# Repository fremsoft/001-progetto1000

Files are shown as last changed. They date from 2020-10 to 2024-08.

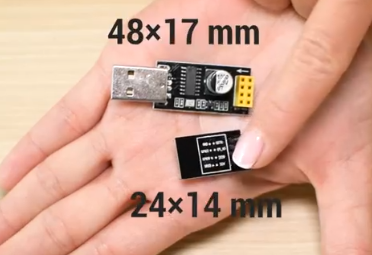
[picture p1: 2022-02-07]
Doc/WIFI/esp-usb.png

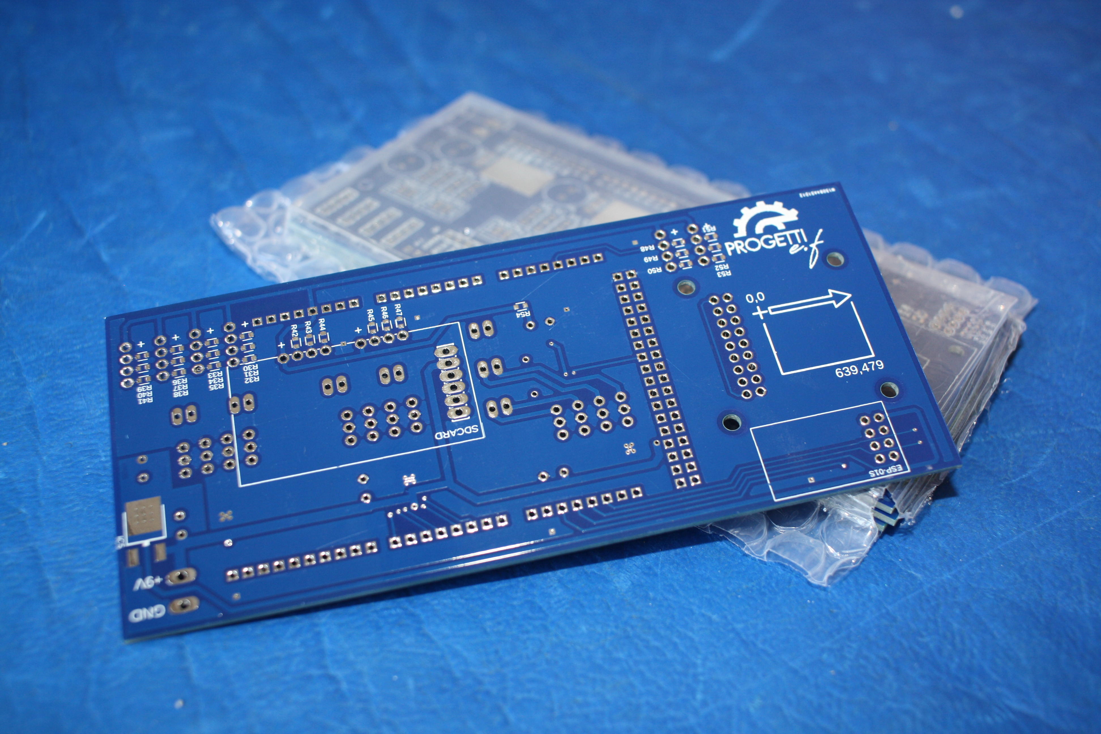
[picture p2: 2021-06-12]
Fusion360/Shield-p1000-2021-05-20/Doc/p1000_bottom.jpg

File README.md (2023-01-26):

# #progetto1000 il Robot che risolve il Cubo di Rubik
Questo è il primo progetto del [:arrow_forward: Canale YouTube "PROGETTI con Emanuele Frisoni"](https://youtube.com/c/fremsoft), un progetto collaborativo che nasce al raggiungimento di 1000 iscritti: [:movie_camera: Guarda la Playlist completa del progetto](https://www.youtube.com/watch?v=VcB0eAnL97o&list=PLxAafib4pWc7LSfuXC9RSEif6I1dyx5FP)

1. [Parte la progettazione in Live Streaming su Twitch](README.md#parte-la-progettazione-in-live-streaming-su-twitch)
2. [Definizione delle specifiche](README.md#definizione-delle-specifiche)
3. [Attività da svolgere e svolte](README.md#attivit%C3%A0-da-svolgere-e-svolte)
4. [Codici sorgenti](README.md#codici-sorgenti)
5. [Sostieni PROGETTO1000](README.md#sostieni-progetto1000)
6. [Lista della spesa](README.md#lista-della-spesa)

   6.1 [Attrezzature da laboratorio e Kit](README.md#attrezzature-da-laboratorio-e-kit)
   
   6.2 [Materiale e schede elettroniche](README.md#materiale-e-schede-elettroniche)
   
   6.3 [Materiale vario per assemblaggio prototipo](README.md#materiale-vario-per-assemblaggio-prototipo)

## Parte la progettazione in Live Streaming su Twitch
**Ogni Giovedì sera alle 22:00** ci incontriamo su [Twitch Tv](https://www.twitch.tv/fremsoft) per progettare insieme il Robot che risolve il Cubo di Rubik, partendo da zero. Affronteremo tutti i passaggi in maniera approfondita. Ho deciso di utilizzare tecnologie che conosco "per sentito dire", ma su cui non ho mai lavorato. In questo modo vedrai tutto il processo che sta dietro alla ricerca di una soluzione. A differenza di altri progetti che trovi in rete, #progetto1000 non esiste ancora, lo possiamo creare insieme. 

Lo scopo non è mostrare al mondo quanto siamo bravi, ma mostrare agli aspiranti progettisti quali sono tutte le difficoltà che potranno incontrare nel loro percorso e suggerire un modo per affrontarle e superarle.

:clapper: Canale Twitch:  [https://www.twitch.tv/fremsoft](https://www.twitch.tv/fremsoft)

[^ Torna su](README.md#progetto1000-il-robot-che-risolve-il-cubo-di-rubik)

## Definizione delle specifiche
Siccome si tratta di un progetto collaborativo, per definire le specifiche di progetto sono stati fatti alcuni sondaggi esplorativi per determinare quali tecnologie utilizzare in questo primo progetto. I risultati del sondaggio sono i seguenti:

1. Arduino o Microchip PIC? **ARDUINO** [4 voti / 2]

2. Encoder Ottico o Accelerometro Gravitazionale? **ENCODER OTTICO** [3 voti / 1]

3. Costruzioni LEGO o Particolari stampati con Stampante 3D? **STAMPA 3D** [3 voti / 4]

4. Stand alone o Connesso a un PC/Smartphone? **SIA STANDALONE CHE COMANDATO** [4 voti / 4]

5. Muto o Sonoro? **SONORO** [3 voti / 4]

6. Cieco o con Telecamera? **TELECAMERA** [0 voti / 4]

7. Procedurale o Intelligenza Artificiale? **A.I.** [0 voti / 5 ]

[^ Torna su](README.md#progetto1000-il-robot-che-risolve-il-cubo-di-rubik)

## Attività da svolgere e svolte
Ogni progetto che si rispetti deve prevedere una serie di fasi da svolgere. Maggiore sarà la difficoltà del progetto e maggiori sono le incognite, tanto più sarà difficile riuscire a prevedere con esattezza tutte le fasi. Ciononostante, è sempre buona norma prevedere con la massima accuratezza tutte le fasi del progetto in una sorta di planning. Ad ogni modo il progetto può essere periodicamente rivisitato, modificato e corretto, in corso d'opera.

L'utilità di suddividere il progetto in attività elementari, consente al progettista di avere un approccio più razionale ed evitare di disperdersi. Inoltre, laddove sia possibile lavorare in Team, la suddivisione del progetto in attività consente di stabilire se alcune attività possano essere svolte simultaneamente da più attori, per esempio dopo aver definito le specifiche di progetto con precisione, si può affidare il progetto meccanico ad un Team ed il progetto elettronico ad un altro Team di sviluppatori.

- [x] [Analisi di fattibilità](https://youtu.be/We6UntzGp7k)
- [x] Raccolta della documentazione e prove sperimentali con prototipi
  - [x] Dimensioni meccaniche e forze necessarie a manipolare il cubo di Rubik
  - [x] Caratteristiche elettriche e meccaniche dei motori c.c.
  - [x] Caratteristiche elettriche del driver (ponte-H) per motori c.c.
  - [x] Specifiche elettriche dei sensori ottici (fotoresistori/TCUT1350x01)
  - [x] Funzionamento di Arduino (uscite PWM, uscite parallele, timers)
  - [x] DAC e amplificatore audio per speaker 8 ohm
  - [x] Slot per Micro SD Card per Arduino per storage file audio
  - [x] Funzionamento Chip Camera OV7670 e acquisizione immagini
  - [x] Ottica del sensore OV7670
  - [x] Funzionamento del modulo WiFi per comunicazione con Smartphone
  - [x] Alimentazione 5V @ 10A
  - [-] ~~Selezione molle per mano robotica~~
- [x] Progettazione meccanica 
  - [x] Realizzazione delle parti che compongono il Robot (esportati in STL)
  - [x] Stampare in 3D le componenti meccaniche
  - [x] Assemblare le parti meccaniche con le parti elettriche (motori, encoder, etc)
- [x] Progettazione elettronica
   - [x] Alimentazione
   - [x] Shield p1000 
     - [x] DAC e Amplificatore per altoparlante
     - [x] Modulo SD-Card
     - [x] Interfacciamento Chip Camera OV7670
     - [x] Modulo WiFi
     - [x] Circuiti di condizionamento dei sensori ottici
     - [x] Comando motori
     - [x] Protezioni e filtri EMC/EMI
     - [x] Montare i componenti elettronici
     - [x] Collaudo generale dell'elettronica
- [ ] Progettazione del programma su Arduino
  - [ ] Movimentazione elementare (attraverso la porta seriale invieremo i comandi per eseguire i movimenti)
  - [ ] Acquisizione delle immagini da telecamera per distinguere i colori e mappare gli elementi del cubo di Rubik
  - [ ] Implementare gli algoritmi del metodo CFOP semplificato
    - [ ] Croce bianca
    - [ ] Faccia bianca e primo strato
    - [ ] Secondo strato
    - [ ] Croce gialla
    - [ ] OLL
    - [ ] PLL (primo passaggio)
    - [ ] PLL (secondo passaggio)
    - [ ] Allineamento terzo strato 
  - [ ] Implementare i suoni
- [ ] Progettazione della rete neurale
  - [ ] Addestramento di una rete neurale per riconoscere tutti gli OLL e PLL
  - [ ] Implementazione della rete neurale nell'algoritmo 
- [ ] Progettazione dell'applicativo per Android per mescolare il cubo con una specifica scramble o altro (forse questa fase salta)
- [ ] Dare un nome al robot

[^ Torna su](README.md#progetto1000-il-robot-che-risolve-il-cubo-di-rubik)

## Codici sorgenti
**#progetto1000** è un progetto Open-Source collaborativo. Tutti i sorgenti elaborati in fase di progettazione sono presenti su questo canale GitHub. Esplora le cartelle di [001-progetto1000](https://github.com/fremsoft/001-progetto1000) e troverai i sorgenti del progetto meccanico, elettronico, software e altro materiale prodotto in fase di progettazione.

Il codice sorgente di **Arduino** sarà disponibile anche a questo link: [Sorgenti Arduino](https://create.arduino.cc/editor/fremsoft/6501effc-6729-46f5-a2f1-0bfa0e9eb691/preview)

La Shield #P1000 è stata omaggiata da [PcbWay.com](https://www.pcbway.com/setinvite.aspx?inviteid=15084) che è sponsor ufficiale di Progetto 1000. Trovi il progetto del PCB scaricabile anche qui: [Shield #P1000 su PcbWay](https://www.pcbway.com/project/shareproject/Shield__P1000__for_Arduino_Mega.html), ricordati di votare il progetto!

[^ Torna su](README.md#progetto1000-il-robot-che-risolve-il-cubo-di-rubik)

## Sostieni PROGETTO1000 
Se **#progetto1000** ti sta appassionando e desideri sostenere la progettazione, puoi acquistare i componenti necessari alla creazione del prototipo o le attrezzature necessarie all'allestimento del laboratorio, facendoli recapitare al mio indirizzo. La lista dei desideri completa dove trovi tutte le cose che servono:

:notebook: "Wish list Amazon" - https://amzn.to/2BDtwIV

Un altro modo per sostenere il canale è seguendo il [canale YouTube](https://youtube.com/c/fremsoft), semplicemente guardando i video, iscrivendoti al canale, mettendo like e interagendo con i commenti, ma soprattutto condividendo i video che preferisci con i tuoi amici progettisti, sono tutti modi per sostenere gratuitamente il canale.

[^ Torna su](README.md#progetto1000-il-robot-che-risolve-il-cubo-di-rubik)

## Lista della spesa
**#progetto1000** sta nascendo, non abbiamo ancora una BOM (Bill Of Material), ma stiamo già acquistando un po' di materiale per realizzare il prototipo e fare le prime prove pratiche. Se vuoi sviluppare insieme a noi e vuoi eseguire le stesse prove a casa tua, ti indico quale materiale ho acquistato qui di seguito:

### Attrezzature da laboratorio e Kit
* [Kit Elettronico con breadboard](https://amzn.to/2QTgOw7)
* [Super Starter Kit UNO project](https://amzn.to/2QJrnNc)
* [Calibro digitale](https://amzn.to/36QMR6w)
* [Bilancia digitale](https://amzn.to/3nxseCa)

### Materiale e schede elettroniche
* [Arduino Mega 2560](https://amzn.to/30RCvj6)
* [Telecamera a colori per Arduino](https://amzn.to/3nbS0Ma)
* [Set 6 motori con accessori](https://amzn.to/3nhQrfy)
* [Fotoresistore](https://amzn.to/370EtBg)
* [Shield #P1000 su PcbWay](https://www.pcbway.com/project/shareproject/Shield__P1000__for_Arduino_Mega.html)

### Materiale vario per assemblaggio prototipo
* [Sfere in acciaio 4mm](https://amzn.to/3lzfDwr)

Trovi la lista completa al seguente link:
🛒 [Lista della spesa di #progetto1000](https://www.amazon.it/hz/wishlist/ls/8D7WPLCAZ7KL?tag=p-ef-21)

[^ Torna su](README.md#progetto1000-il-robot-che-risolve-il-cubo-di-rubik)

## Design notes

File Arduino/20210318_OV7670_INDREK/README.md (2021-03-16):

Queste sono alcune immagini catturate dalla Chip Camera OV7670 e salvate in formato HTML per essere visualizzate da un qualsiasi browser.

Finalmente riusciamo a distinguere qualcosa, le immagini sono parecchio sfocate ma siamo sulla buona strada:

1. [160x120_cubo_mischiato.htm](http://htmlpreview.github.io/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)

2. [160x24_cubo_1.htm](http://htmlpreview.github.io/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)

3. [160x24_cubo_2.htm](http://htmlpreview.github.io/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)
 
4. [160x24_cubo_3.htm](http://htmlpreview.github.io/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)

5. [160x24_cubo_azzurro.htm](http://htmlpreview.github.io/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)
 
6. [160x24_cubo_rosso.htm](http://htmlpreview.github.io/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)

7. [img1.htm](http://htmlpreview.github.io/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)

8. [img2.htm](http://htmlpreview.github.io/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)

9. [img3.htm](http://htmlpreview.github.io/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)

10. [img4.htm](http://htmlpreview.github.io/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)

11. [img5.htm](http://htmlpreview.github.io/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)

12. [img6.htm](http://htmlpreview.github.io/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)

13. [img7.htm](http://htmlpreview.github.io/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)

14. [img8.htm](http://htmlpreview.github.io/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)

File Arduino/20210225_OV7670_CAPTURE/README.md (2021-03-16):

Queste sono alcune immagini catturate dalla Chip Camera OV7670 e salvate in formato HTML per essere visualizzate da un qualsiasi browser.

Come ben visibile dal risultato prodotto, dobbiamo ancora lavorarci su affinché possiamo ottenere delle immagini accettabili:

1. [img.html](http://htmlpreview.github.io/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)

2. [blue.html](http://htmlpreview.github.io/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)

3. [nero.html](http://htmlpreview.github.io/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)

4. [rosso.html](http://htmlpreview.github.io/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)

5. [panna.html](http://htmlpreview.github.io/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)

6. [progetti.html](http://htmlpreview.github.io/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)

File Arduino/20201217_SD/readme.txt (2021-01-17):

Per usare questo Sketch occorre il MicroSD Card Adapter a slitta:

"Il Manuale di Arduino (Paolo Aliverti)" - https://amzn.to/39o6DaB
"Scheda Micro SD per Arduino" - https://amzn.to/34uBorh
"Micro SD Card 16 GB" - https://amzn.to/34y9N8x
"USB to SD Card Adapter" - https://amzn.to/2LZ575r

Vedi lo schema e la procedura qui: https://youtu.be/E36JJB-z9BE

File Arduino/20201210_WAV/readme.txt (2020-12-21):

Per usare questo Sketch occorre realizzare un DAC con 
rete a partitore resistivo R-2R sui pin 42(MSb)÷49(LSb)
di Arduino Mega.

Vedi lo schema qui: https://youtu.be/YSctt-mZF6c

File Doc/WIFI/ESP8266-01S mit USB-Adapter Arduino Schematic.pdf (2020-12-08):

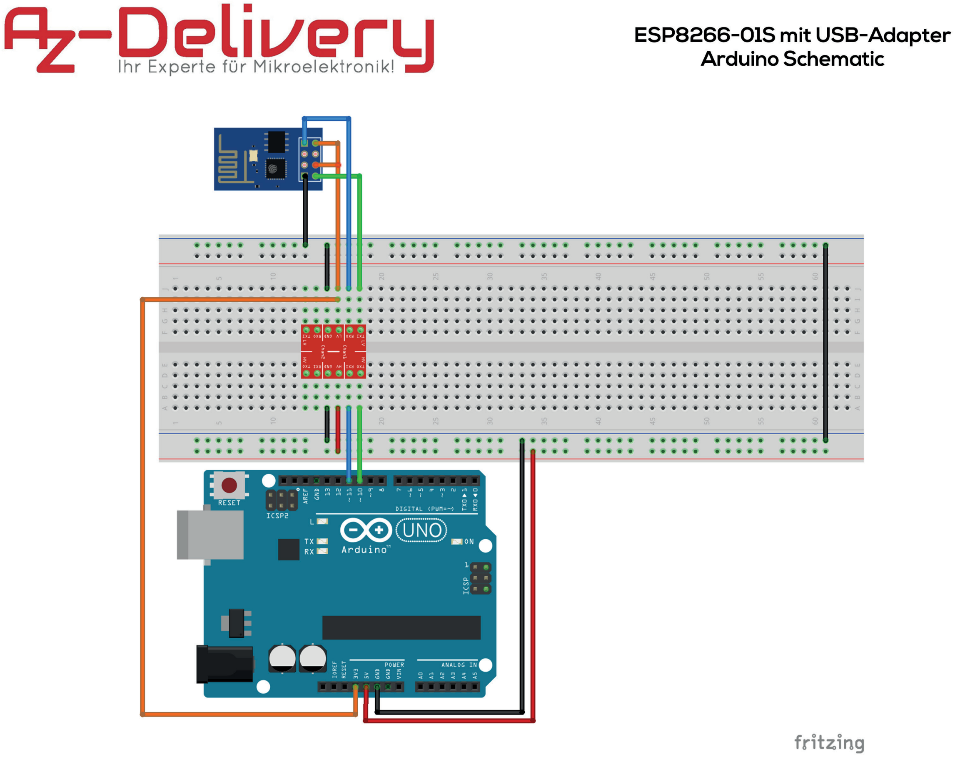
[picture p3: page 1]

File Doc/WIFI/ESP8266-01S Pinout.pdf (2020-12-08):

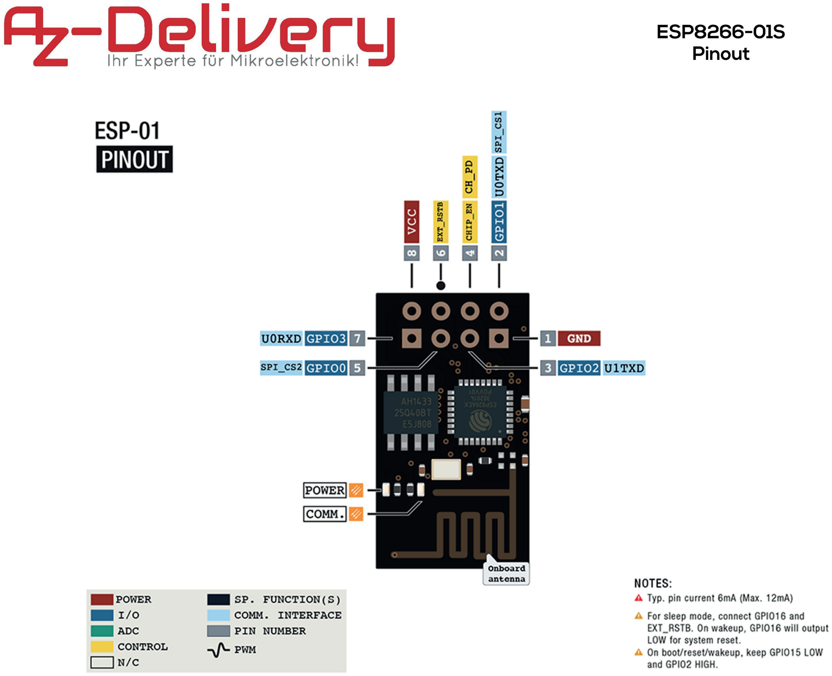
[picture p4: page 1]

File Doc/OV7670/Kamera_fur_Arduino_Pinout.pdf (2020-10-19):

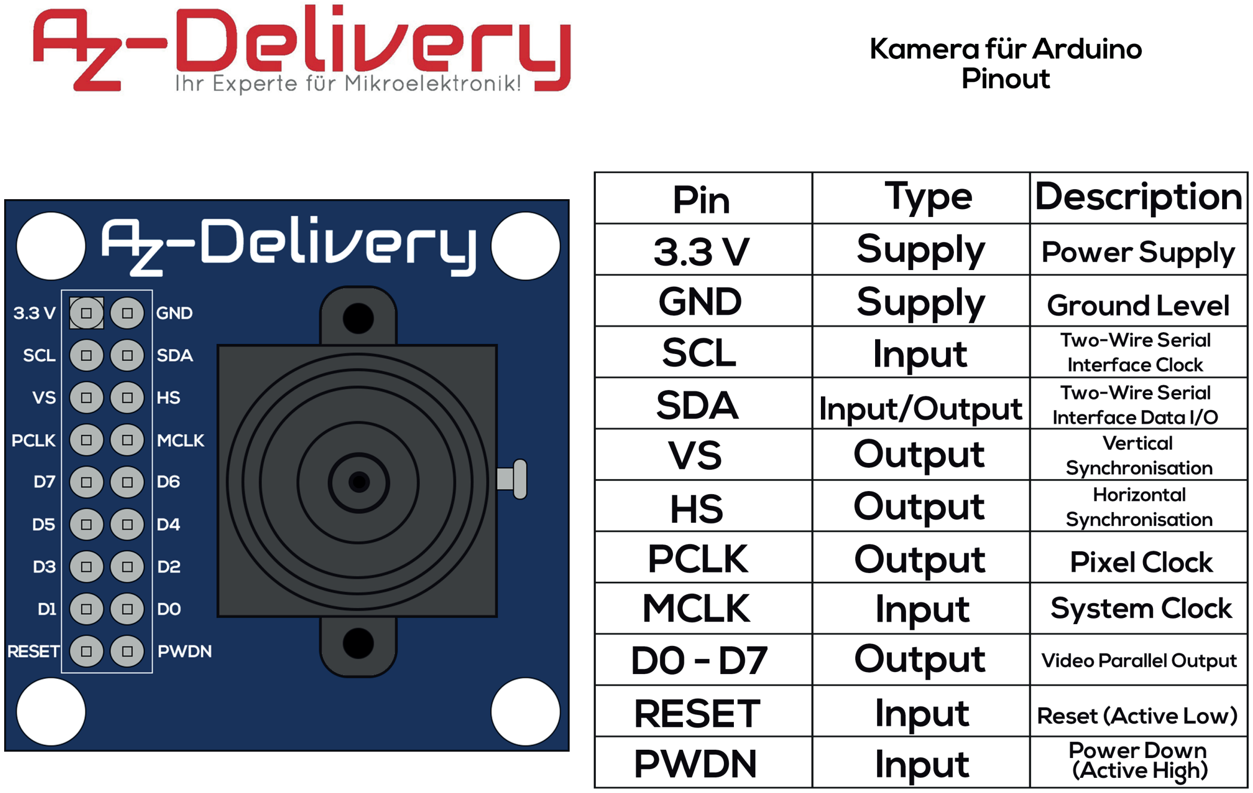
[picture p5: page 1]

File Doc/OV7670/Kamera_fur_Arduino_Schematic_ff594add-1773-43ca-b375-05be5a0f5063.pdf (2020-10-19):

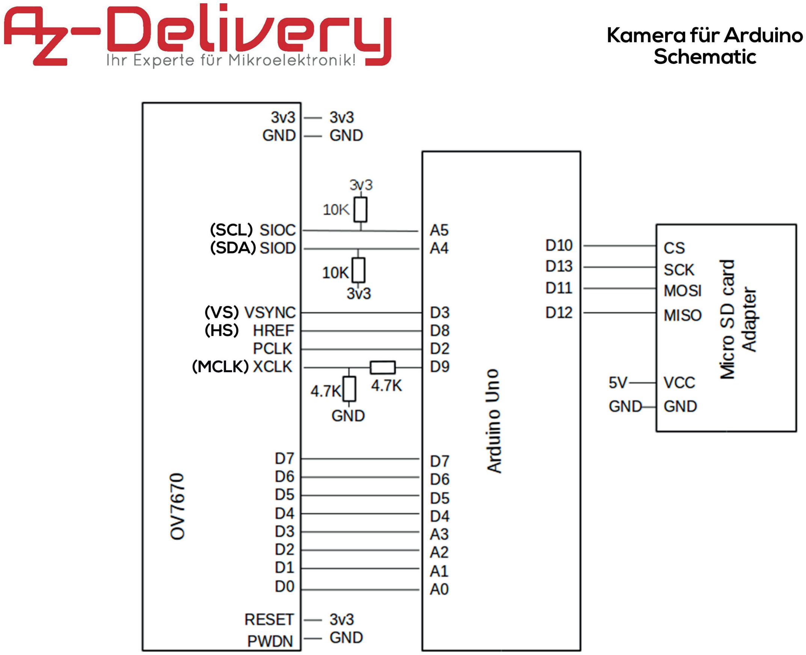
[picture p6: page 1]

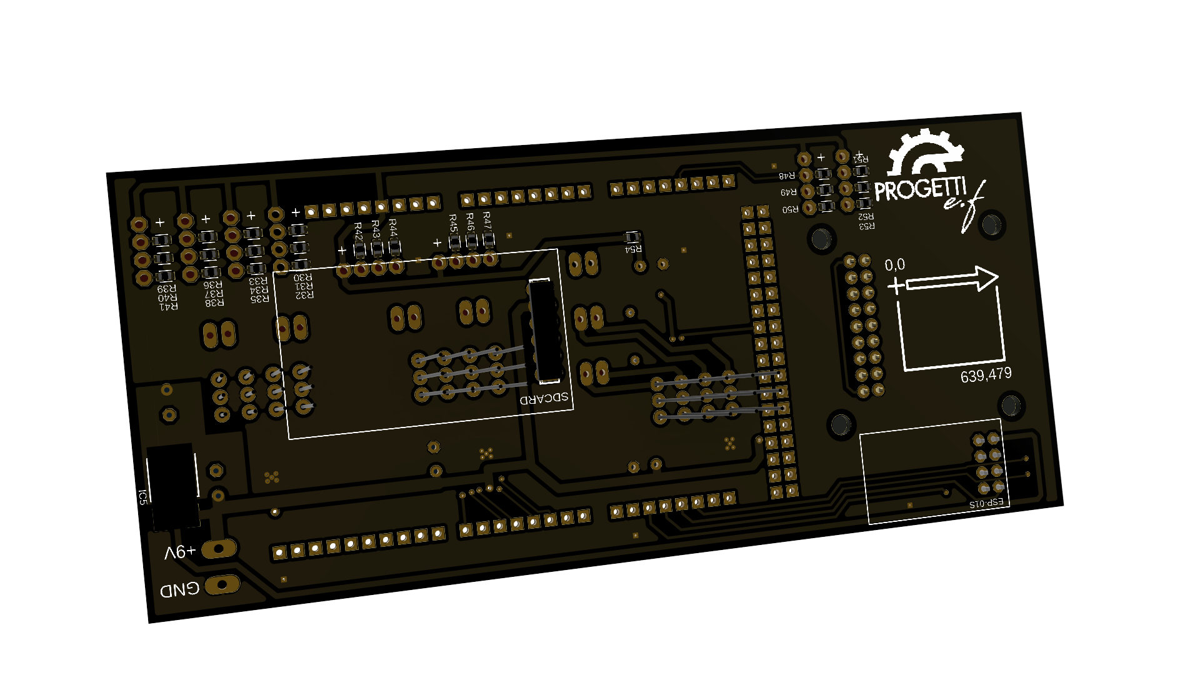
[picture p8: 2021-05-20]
Fusion360/Shield-p1000-2021-05-20/Doc/shield-p1000-render-bot.png

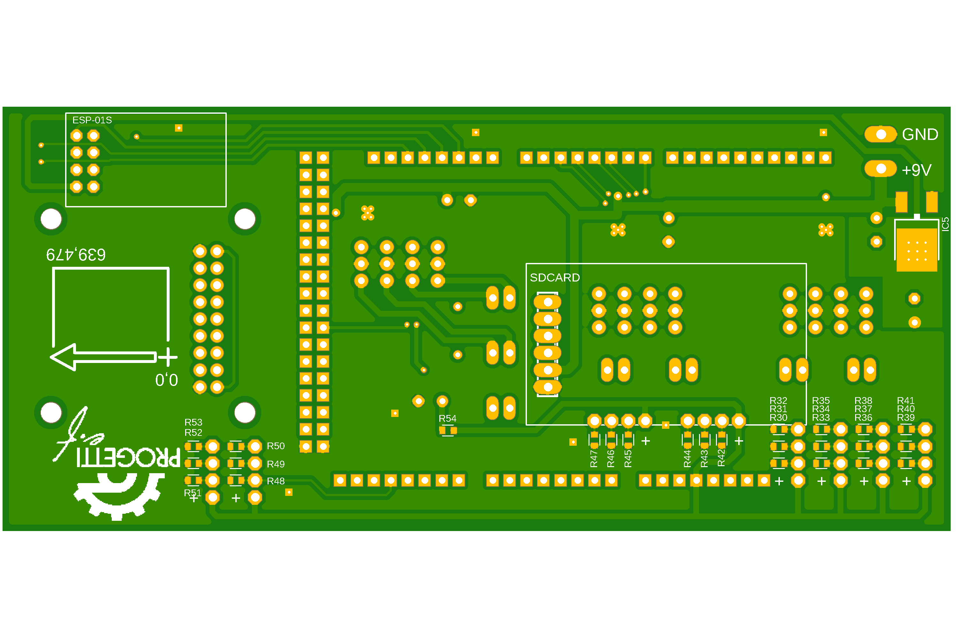
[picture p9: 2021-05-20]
Fusion360/Shield-p1000-2021-05-20/Doc/shield-p1000-bot.png

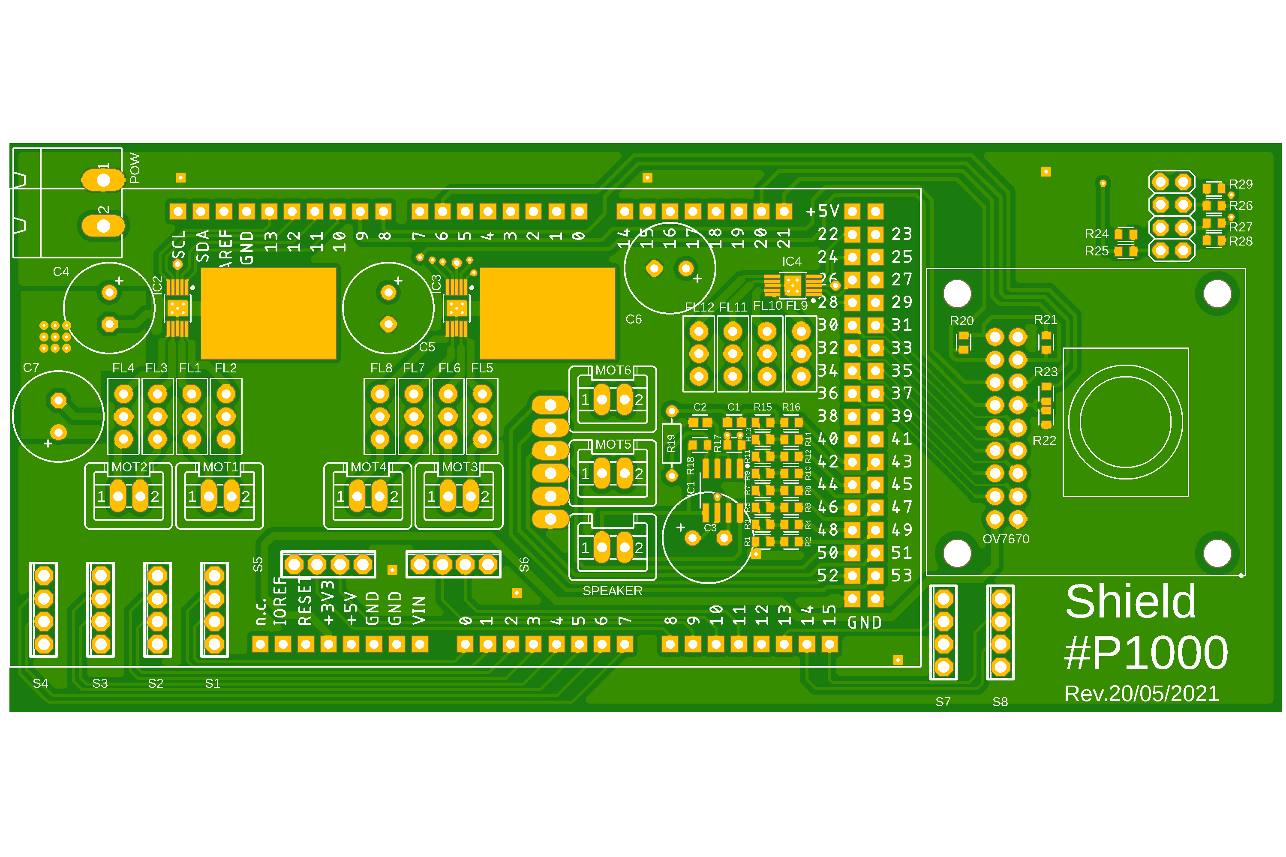
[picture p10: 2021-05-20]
Fusion360/Shield-p1000-2021-05-20/Doc/shield-p1000-top.png

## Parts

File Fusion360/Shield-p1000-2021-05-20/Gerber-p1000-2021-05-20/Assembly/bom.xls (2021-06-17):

 | QUANTITY | PARTS | VALUE | DESCRIPTION | PACKAGE | URL
PTH
 | 10 | ARDUINO MEGA | 77311-820-36LF | CONN HEADER VERT 10POS 2.54MM L=20mm | 10 x 2,54 mm HEADER | https://www.digikey.it/product-detail/it/amphenol-icc-fci/77311-820-36LF/609-77311-820-36LF-ND/4404923
 | 4 | C3, C4, C5, C6 | 220 uF | CAP 220 UF 20% 35 V | D=10mm sp=3.5mm | https://www.digikey.it/product-detail/it/w%C3%BCrth-elektronik/860040574006/732-9217-1-ND/5729160
 | 1 | C7 | 100 uF | CAP 100 UF 20% 50 V | D=10mm sp=3.5mm | https://www.digikey.it/product-detail/it/w%C3%BCrth-elektronik/860010674014/732-8666-1-ND/5728621
 | 1 | ESP-01S | PPTC042LFBN-RC | CONN HDR 8POS 0.1 TIN PCB | 4x2 x 2.54 mm HEADER | https://www.digikey.it/product-detail/it/sullins-connector-solutions/PPTC042LFBN-RC/S7072-ND/810211
 | 12 | FL1, FL2, FL3, FL4, FL5, FL6, FL7, FL8, FL9, FL10, FL11, FL12 | DSS1NB32A101Q91A | FILTER LC(T) 100PF TH | PTH 3 x 2.54 MM | https://www.digikey.it/product-detail/it/murata-electronics/DSS1NB32A101Q91A/490-9787-1-ND/5018362
 | 7 | MOT1, MOT2, MOT3, MOT4, MOT5, MOT6, SPEAKER | JST-XH | XH-2A (PCB MALE), XH-2Y (FEMALE) | 2 x 2.54 mm HEADER | https://amzn.to/3yEI4QU
 | 1 | OV7670 | PPTC092LFBN-RC | CONN HDR 18POS 0.1 TIN PCB | 9x2 x 2.54 mm HEADER | https://www.digikey.it/product-detail/it/sullins-connector-solutions/PPTC092LFBN-RC/S7077-ND/810215
 | 1 | POWER | TBP01R1-508-02BE | TERMINAL BLOCK, PLUGGABLE, 5.08, PCB | 2 x 5.08 mm | https://www.digikey.it/product-detail/it/cui-devices/TBP01R1-508-02BE/102-6406-ND/10238383
 | 1 | POWER | TBP01P1-508-02BE | TERMINAL BLOCK, PLUGGABLE, 5.08 | 2 x 5.08 mm | https://www.digikey.it/product-detail/it/cui-devices/TBP01P1-508-02BE/102-6390-ND/10238367
 | 1 | R19 | 10 kohm | RES 10K OHM 1/4W 5% AXIAL | 2,30 x 6,00 mm axial ¼ W | https://www.digikey.it/product-detail/it/stackpole-electronics-inc/CF14JT10K0/CF14JT10K0CT-ND/1830374
 | 8 | S1, S2, S3, S4, S5, S6, S7, S8 | JST-XH | XH-4A (PCB MALE), XH-4Y (FEMALE) | 4 x 2.54 mm HEADER | https://amzn.to/3yEI4QU
SMD
 | 2 | C1, C2 | 1 uF | CAP CER 1UF 25V X5R 0603 | CAPC1608X85 | https://www.digikey.it/product-detail/it/samsung-electro-mechanics/CL10A105KA8NNNC/1276-1102-1-ND/3889188
 | 1 | IC1 | LM4889MA | IC AMP CLASS AB MONO 1W 8SOIC | SOIC127P599X175-8N | https://www.digikey.it/product-detail/it/texas-instruments/LM4889MA-NOPB/296-43508-5-ND/947615
 | 3 | IC2, IC3, IC4 | A3909 | IC MOTOR DRIVER PAR 10MSOP | 10-MSOP | https://www.digikey.it/product-detail/it/allegro-microsystems/A3909GLYTR-T/620-1499-1-ND/3979660
 | 1 | IC5 | LD117ADT33TR | LDO VOLTAGE REGULATOR | TO-252-3 DPACK | https://www.digikey.it/product-detail/it/texas-instruments/LM1117IDT-3-3-NOPB/LM1117IDT-3-3-NOPB-ND/482898
 | 9 | R1, R2, R4 ,R6, R8, R10, R12, R14, R16 | 20 kohm | RES 20K OHM 1% 1/10W 0603 | RESC1608X60 | https://www.digikey.it/product-detail/it/stackpole-electronics-inc/RMCF0603FT20K0/RMCF0603FT20K0CT-ND/1943075
 | 1 | R18 | 47 kohm | RES 47K OHM 1% 1/10W 0603 | RESC1608X60 | https://www.digikey.it/product-detail/it/bourns-inc/CR0603-FX-4702ELF/CR0603-FX-4702ELFCT-ND/3925317
 | 4 | R22, R24, R28, R29 | 1.2 kohm | RES SMD 1.2K OHM 1% 1/10W 0603 | RESC1608X60 | https://www.digikey.it/product-detail/it/bourns-inc/CR0603-FX-1201ELF/118-CR0603-FX-1201ELFCT-ND/3925300
 | 4 | R23, R25, R26, R27 | 680 ohm | RES SMD 680 OHM 1% 1/10W 0603 | RESC1608X60 | https://www.digikey.it/product-detail/it/te-connectivity-passive-product/CRGCQ0603F680R/A129686CT-ND/8577518
 | 10 | R3, R5, R7, R9, R11, R13, R15, R17, R20, R21 | 10 kohm | RES SMD 10K OHM 1% 1/4W 0603 | RESC1608X60 | https://www.digikey.it/product-detail/it/rohm-semiconductor/ESR03EZPF1002/RHM10KADCT-ND/1983753
 | 16 | R30, R31, R33, R34. R36, R37, R39, R40, R42, R43, R45, R46, R48, R49, R51, R52 | 4.7 kohm | RES 4.7K OHM 1% 1/10W 0603 | RESC1608X60 | https://www.digikey.it/product-detail/it/bourns-inc/CR0603-FX-4701ELF/CR0603-FX-4701ELFCT-ND/3740884
 | 8 | R32, R35, R38, R41, R44, R47, R50, R53 | 330 ohm | RES SMD 330 OHM 5% 1/10W 0603C | RESC1608X60 | https://www.digikey.it/product-detail/it/te-connectivity-passive-product/CRGCQ0603J330R/A130088CT-ND/8577920
 | 1 | R54 | 10 ohm | RES 10 OHM 1% 1/3W 0603 | RESC1608X60 | https://www.digikey.it/product-detail/it/koa-speer-electronics-inc/SG73P1JTTD10R0F/2019-SG73P1JTTD10R0FCT-ND/13404248
COMPONENTS
 | 1 | ARDUINO MEGA | ARDUINO MEGA | Arduino Mega 2560 R3 |  | https://amzn.to/2SraGMU
 | 1 | ESP-01S | ESP-01S | AZDelivery ESP-01S ESP8266 WiFi Module | 4x2 x 2.54 mm HEADER | https://amzn.to/3yAf5On
 | 2 | CABLE | CABLE | CBL 2COND 18AWG BLACK/RED 1M | 18AWG x 1m | https://www.digikey.it/product-detail/it/tensility-international-corp/30-00415/T1306-1-ND/5638247
 | 6 | CM1, CM2, CM3, CM4, CM5, CM6 | 100 nF | CAP CER 0.1UF 50V X7R AXIAL | AXIAL PTH | https://www.digikey.it/product-detail/it/vishay-beyschlag-draloric-bc-components/A104K15X7RF5TAA/1109PHCT-ND/145913
 | 1 | MICROSD | SD-0128 | AZDelivery MicroSD module | 6 x 2.54 mm HEADER | https://amzn.to/3vkUED2
 | 2 | MOT1, MOT2, MOT3, MOT4, MOT5, MOT6 | DC MOTOR KIT + GEARS | Proster 6 Set DC Motore DIY | 38 x 16 x 19 mm | https://amzn.to/3fIIbCy
 | 1 | OV7670 | OV7670 | AZDelivery OV7670 RGB Chip Camera | 9x2 x 2.54 mm HEADER | https://amzn.to/34cejJs
 | 1 | SPEAKER | SP-4005Y | SPEAKER, 88DB SENSITIVITY, 40MM | 40 mm | https://www.digikey.it/product-detail/it/soberton-inc/SP-4005Y/433-1270-ND/9924431

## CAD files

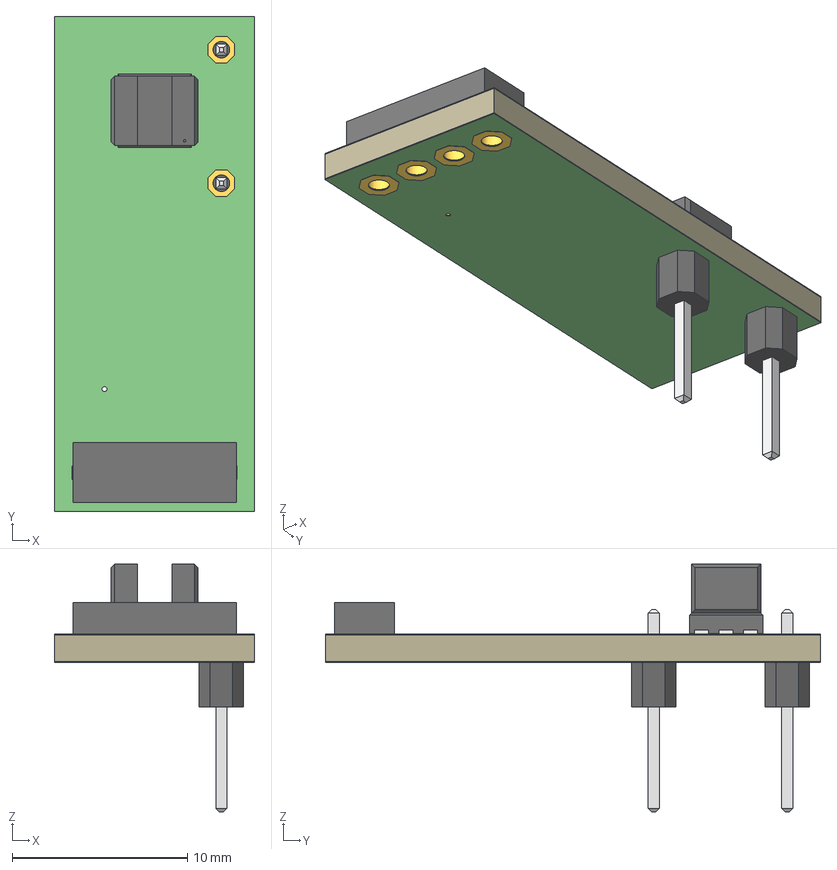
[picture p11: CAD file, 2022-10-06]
Fusion360/Encoder-p1000/ecnoder_TCUT1350 v3.step
11.4 x 28.2 x 14.1 mm
Board
4POL254
1X01 x 2
1-copper
16-copper
1-soldermask
16-soldermask

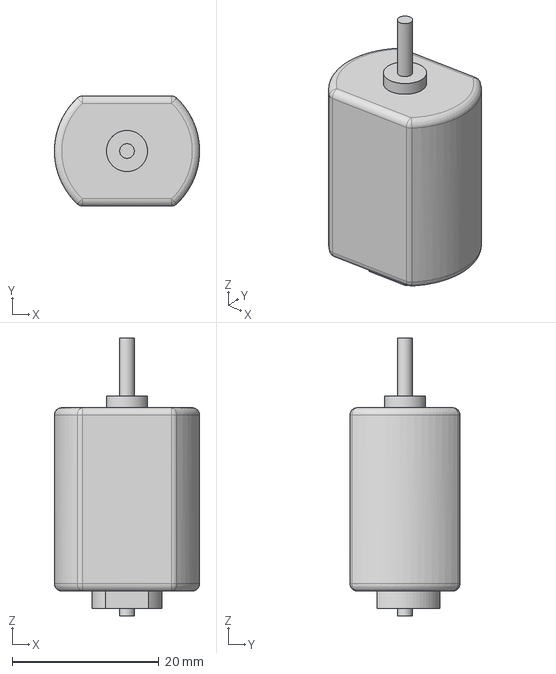
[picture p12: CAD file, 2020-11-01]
Fusion360/Motorino DC 3V v3.igs
19.8 x 15.0 x 37.9 mm

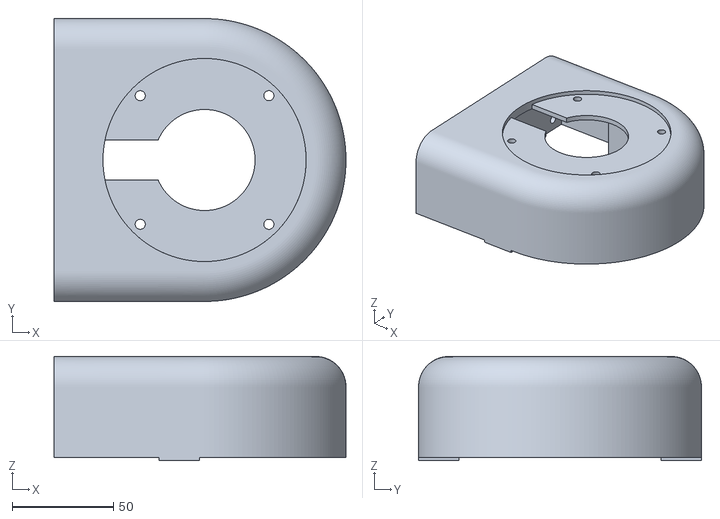
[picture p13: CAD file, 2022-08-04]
Fusion360/Robot_p1000/stl_produzione/basamento robot 2.stl
144.5 x 140.0 x 51.5

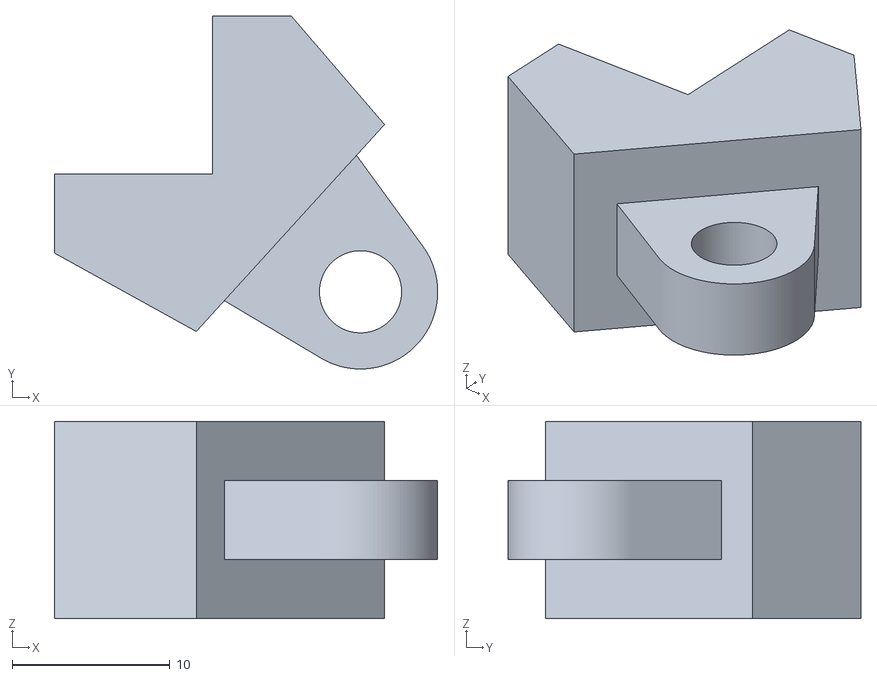
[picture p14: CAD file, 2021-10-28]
Fusion360/stl_mano_robotica/falangetta.stl
24.3 x 22.3 x 12.5

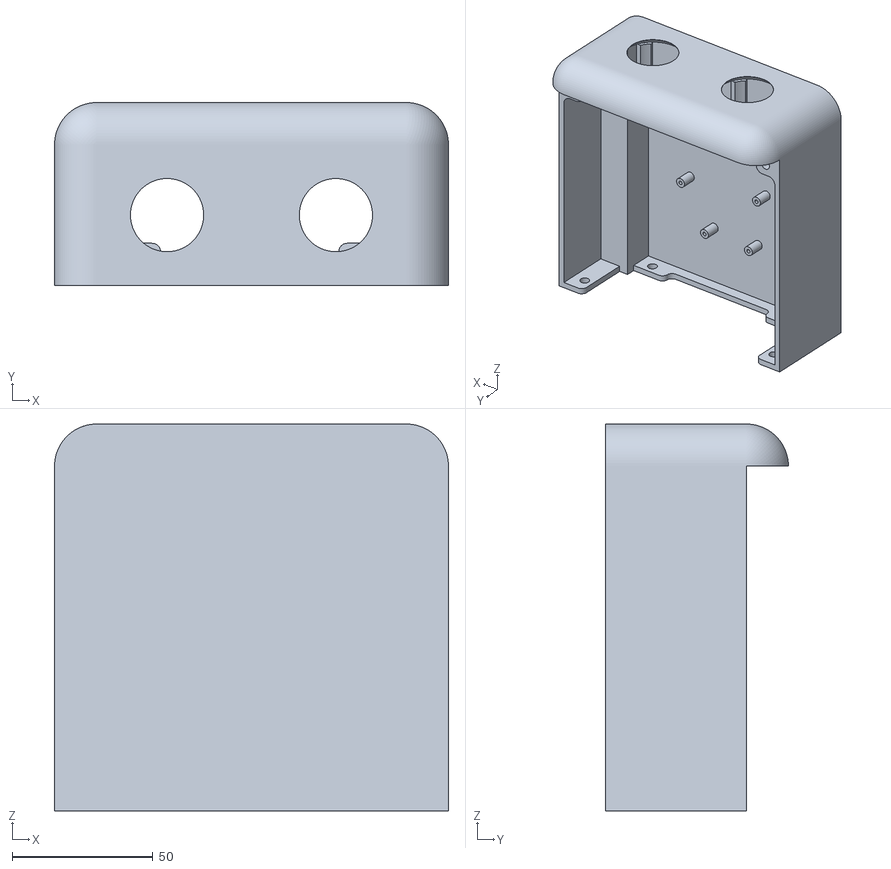
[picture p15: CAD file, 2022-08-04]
Fusion360/Robot_p1000/stl_produzione/basamento robot 5.stl
140.0 x 65.0 x 137.5

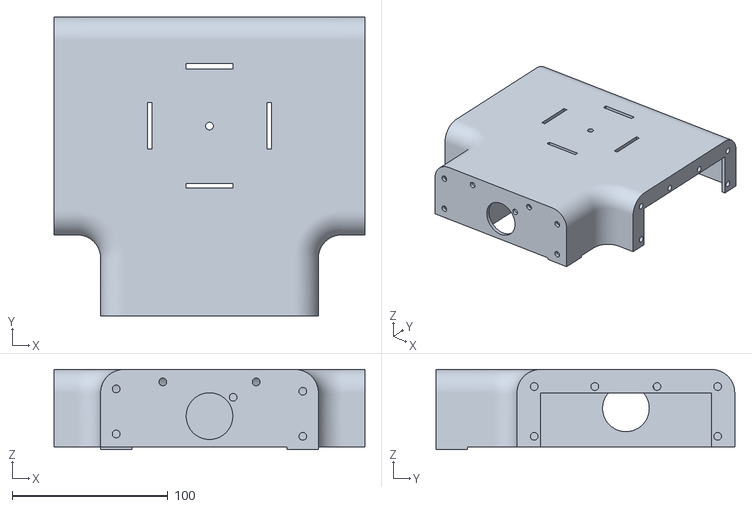
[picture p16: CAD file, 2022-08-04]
Fusion360/Robot_p1000/stl_produzione/basamento robot 1.stl
200.0 x 192.0 x 51.5

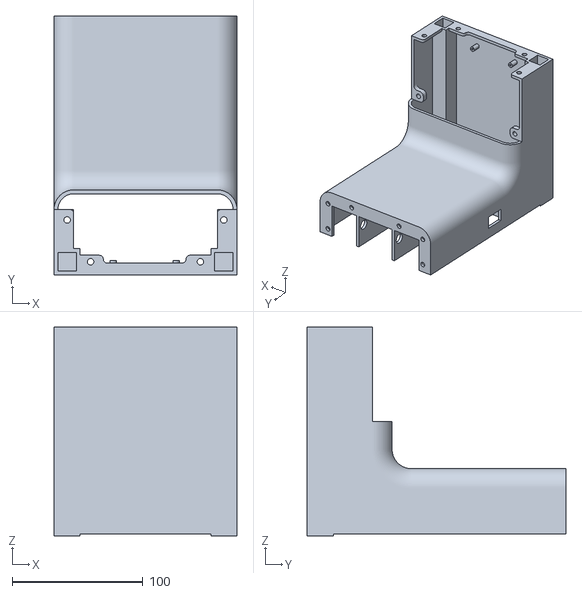
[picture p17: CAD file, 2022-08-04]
Fusion360/Robot_p1000/stl_produzione/basamento robot 4.stl
140.0 x 198.0 x 160.0

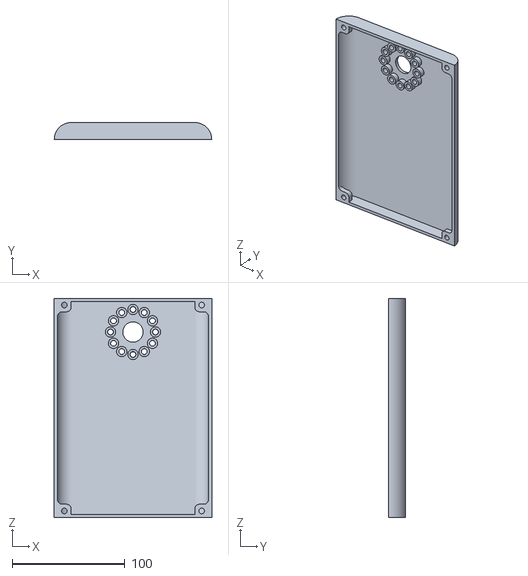
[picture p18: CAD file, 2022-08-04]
Fusion360/Robot_p1000/stl_produzione/basamento robot 6.stl
140.0 x 15.0 x 194.6

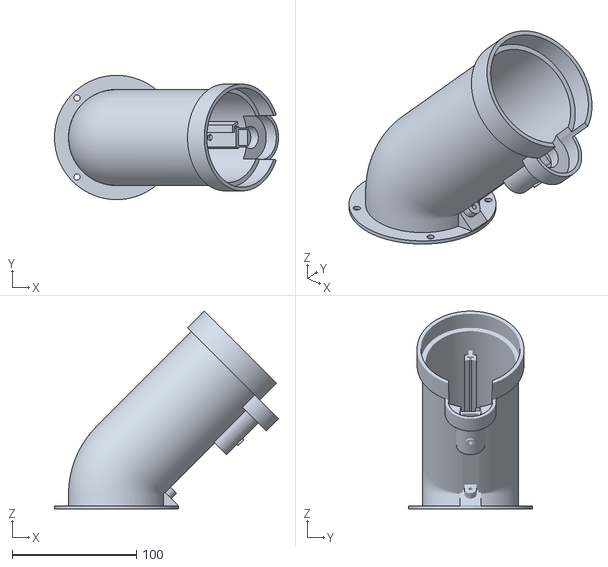
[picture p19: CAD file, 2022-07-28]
Fusion360/Robot_p1000/stl_produzione/braccio.stl
180.3 x 100.0 x 159.2

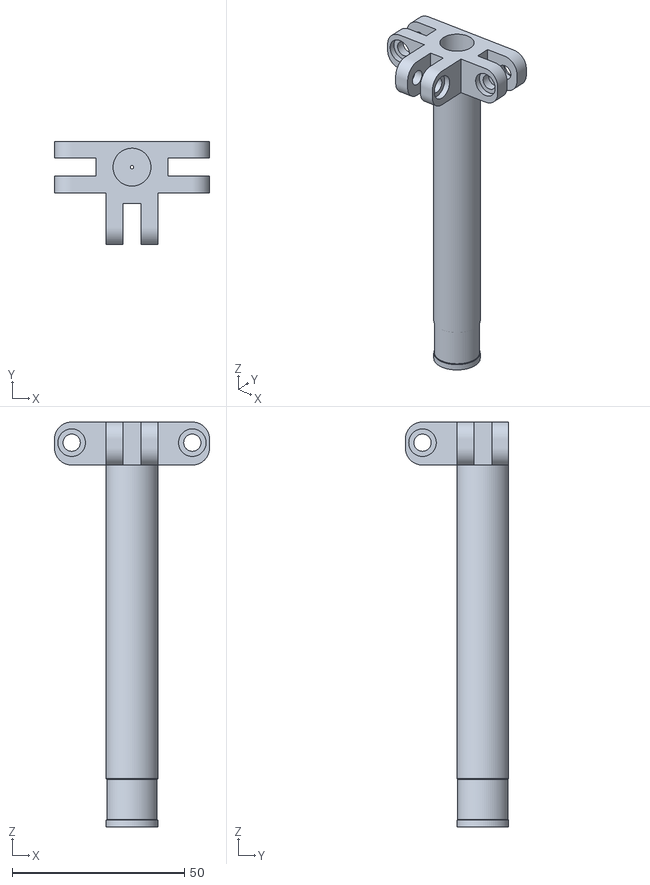
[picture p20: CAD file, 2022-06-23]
Fusion360/Robot_p1000/stl_produzione/martelletto.stl
45.0 x 30.0 x 117.5

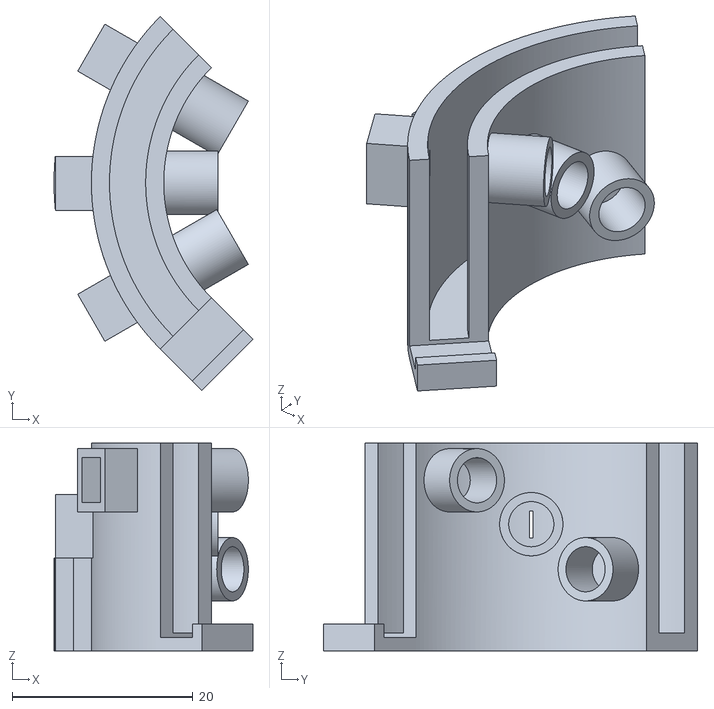
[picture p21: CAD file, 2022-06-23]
Fusion360/Robot_p1000/stl_produzione/mascherino_encoder.stl
22.0 x 41.4 x 23.0

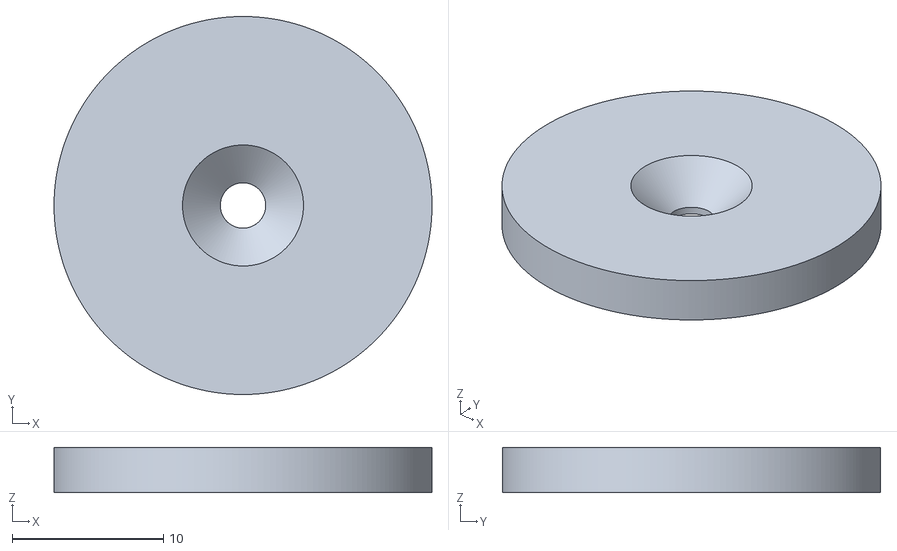
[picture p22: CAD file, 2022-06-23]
Fusion360/Robot_p1000/stl_produzione/rondella-martelletto.stl
25.0 x 25.0 x 3.00

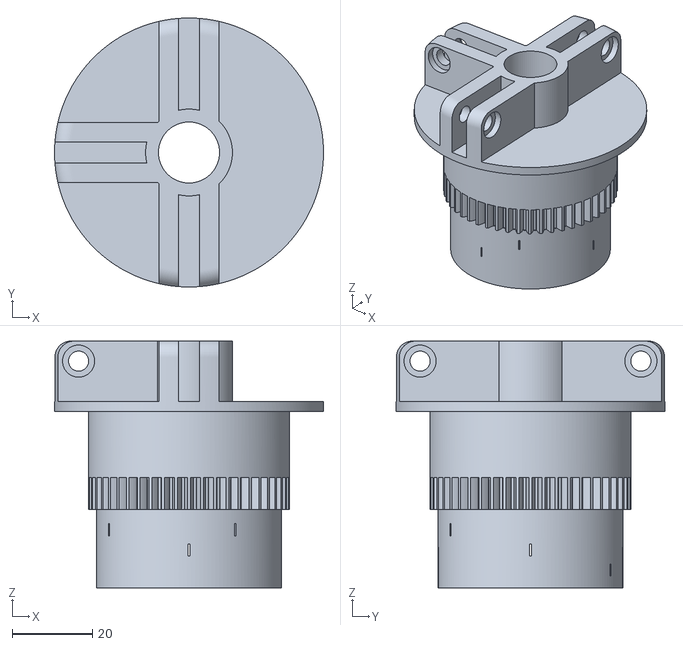
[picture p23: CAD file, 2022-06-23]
Fusion360/Robot_p1000/stl_produzione/base.stl
67.0 x 67.0 x 61.5

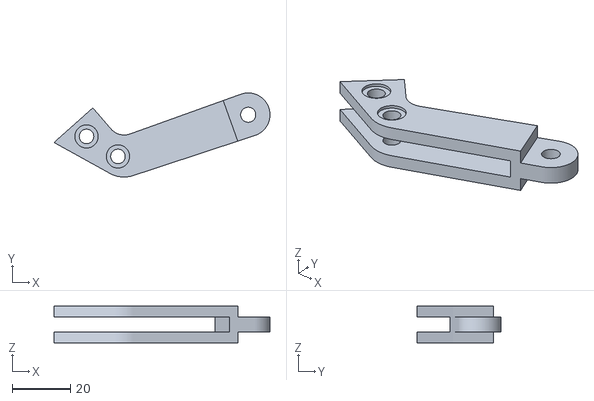
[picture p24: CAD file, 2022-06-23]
Fusion360/Robot_p1000/stl_produzione/dito.stl
74.3 x 28.9 x 12.6

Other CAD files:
Doc/ARDUINO-MEGA-2560/dimensioniMega.dxf
Fusion360/Robot_p1000/stl_produzione/basamento robot 3.stl
Fusion360/Robot_p1000/stl_produzione/puleggia_encoder.stl
Fusion360/Robot_p1000/stl_produzione/braccetto_inferiore.stl
Fusion360/Motorino DC 3V v3.f3d
Fusion360/Robot_p1000/stl_produzione/342682_12mm_hex_wheel.stl
Fusion360/Robot_p1000/stl_produzione/braccetto_dito.stl
Fusion360/Robot_p1000/stl_produzione/cassa_acustica.stl
Fusion360/Robot_p1000/stl_produzione/chiodino_f.stl
Fusion360/Robot_p1000/stl_produzione/chiodino_m.stl
Fusion360/Robot_p1000/stl_produzione/gancino.stl
Fusion360/Robot_p1000/stl_produzione/ingranaggio.stl
Fusion360/Robot_p1000/stl_produzione/seger 4mm.stl

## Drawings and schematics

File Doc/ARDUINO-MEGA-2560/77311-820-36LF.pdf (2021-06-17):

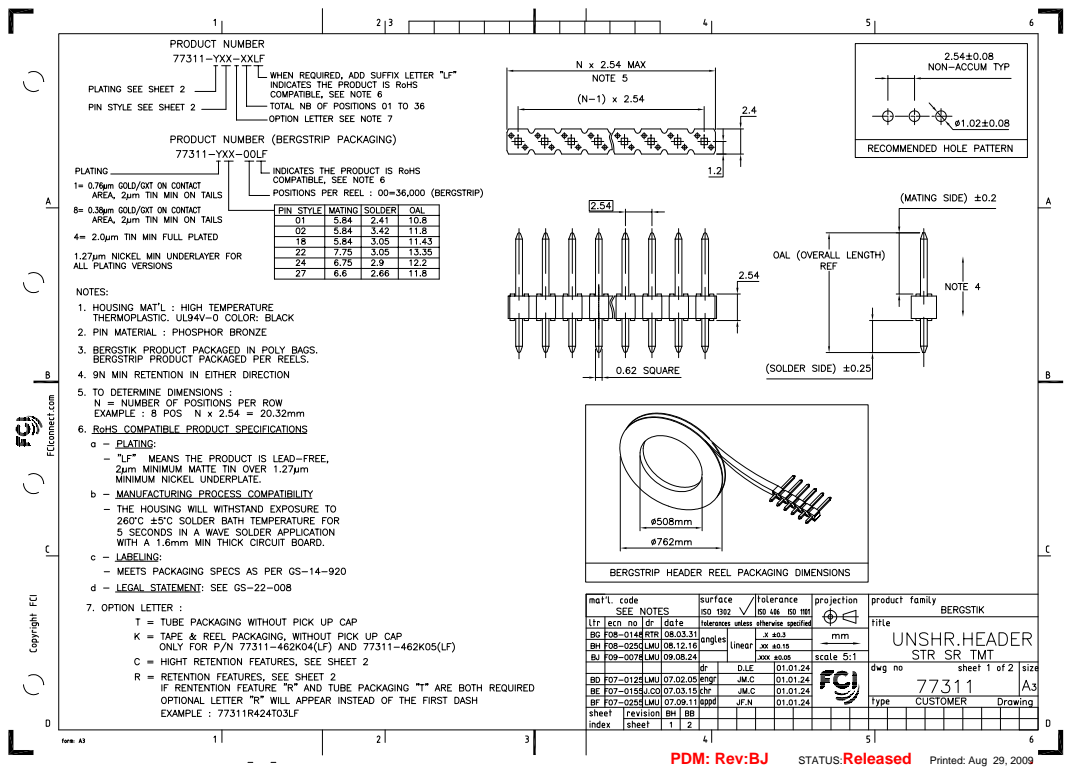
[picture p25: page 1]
PDM: Rev:BJ; Released; . STATUS:; Printed: Aug 29, 2009

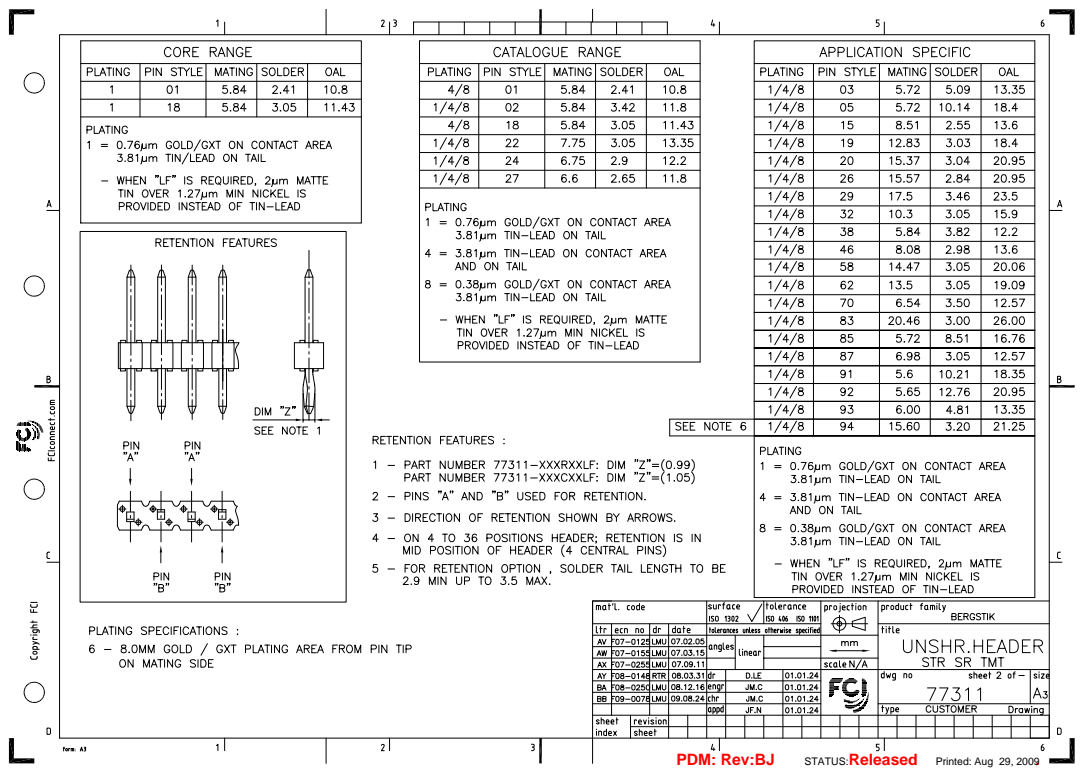
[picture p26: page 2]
PDM: Rev:BJ; Released; . STATUS:; Printed: Aug 29, 2009

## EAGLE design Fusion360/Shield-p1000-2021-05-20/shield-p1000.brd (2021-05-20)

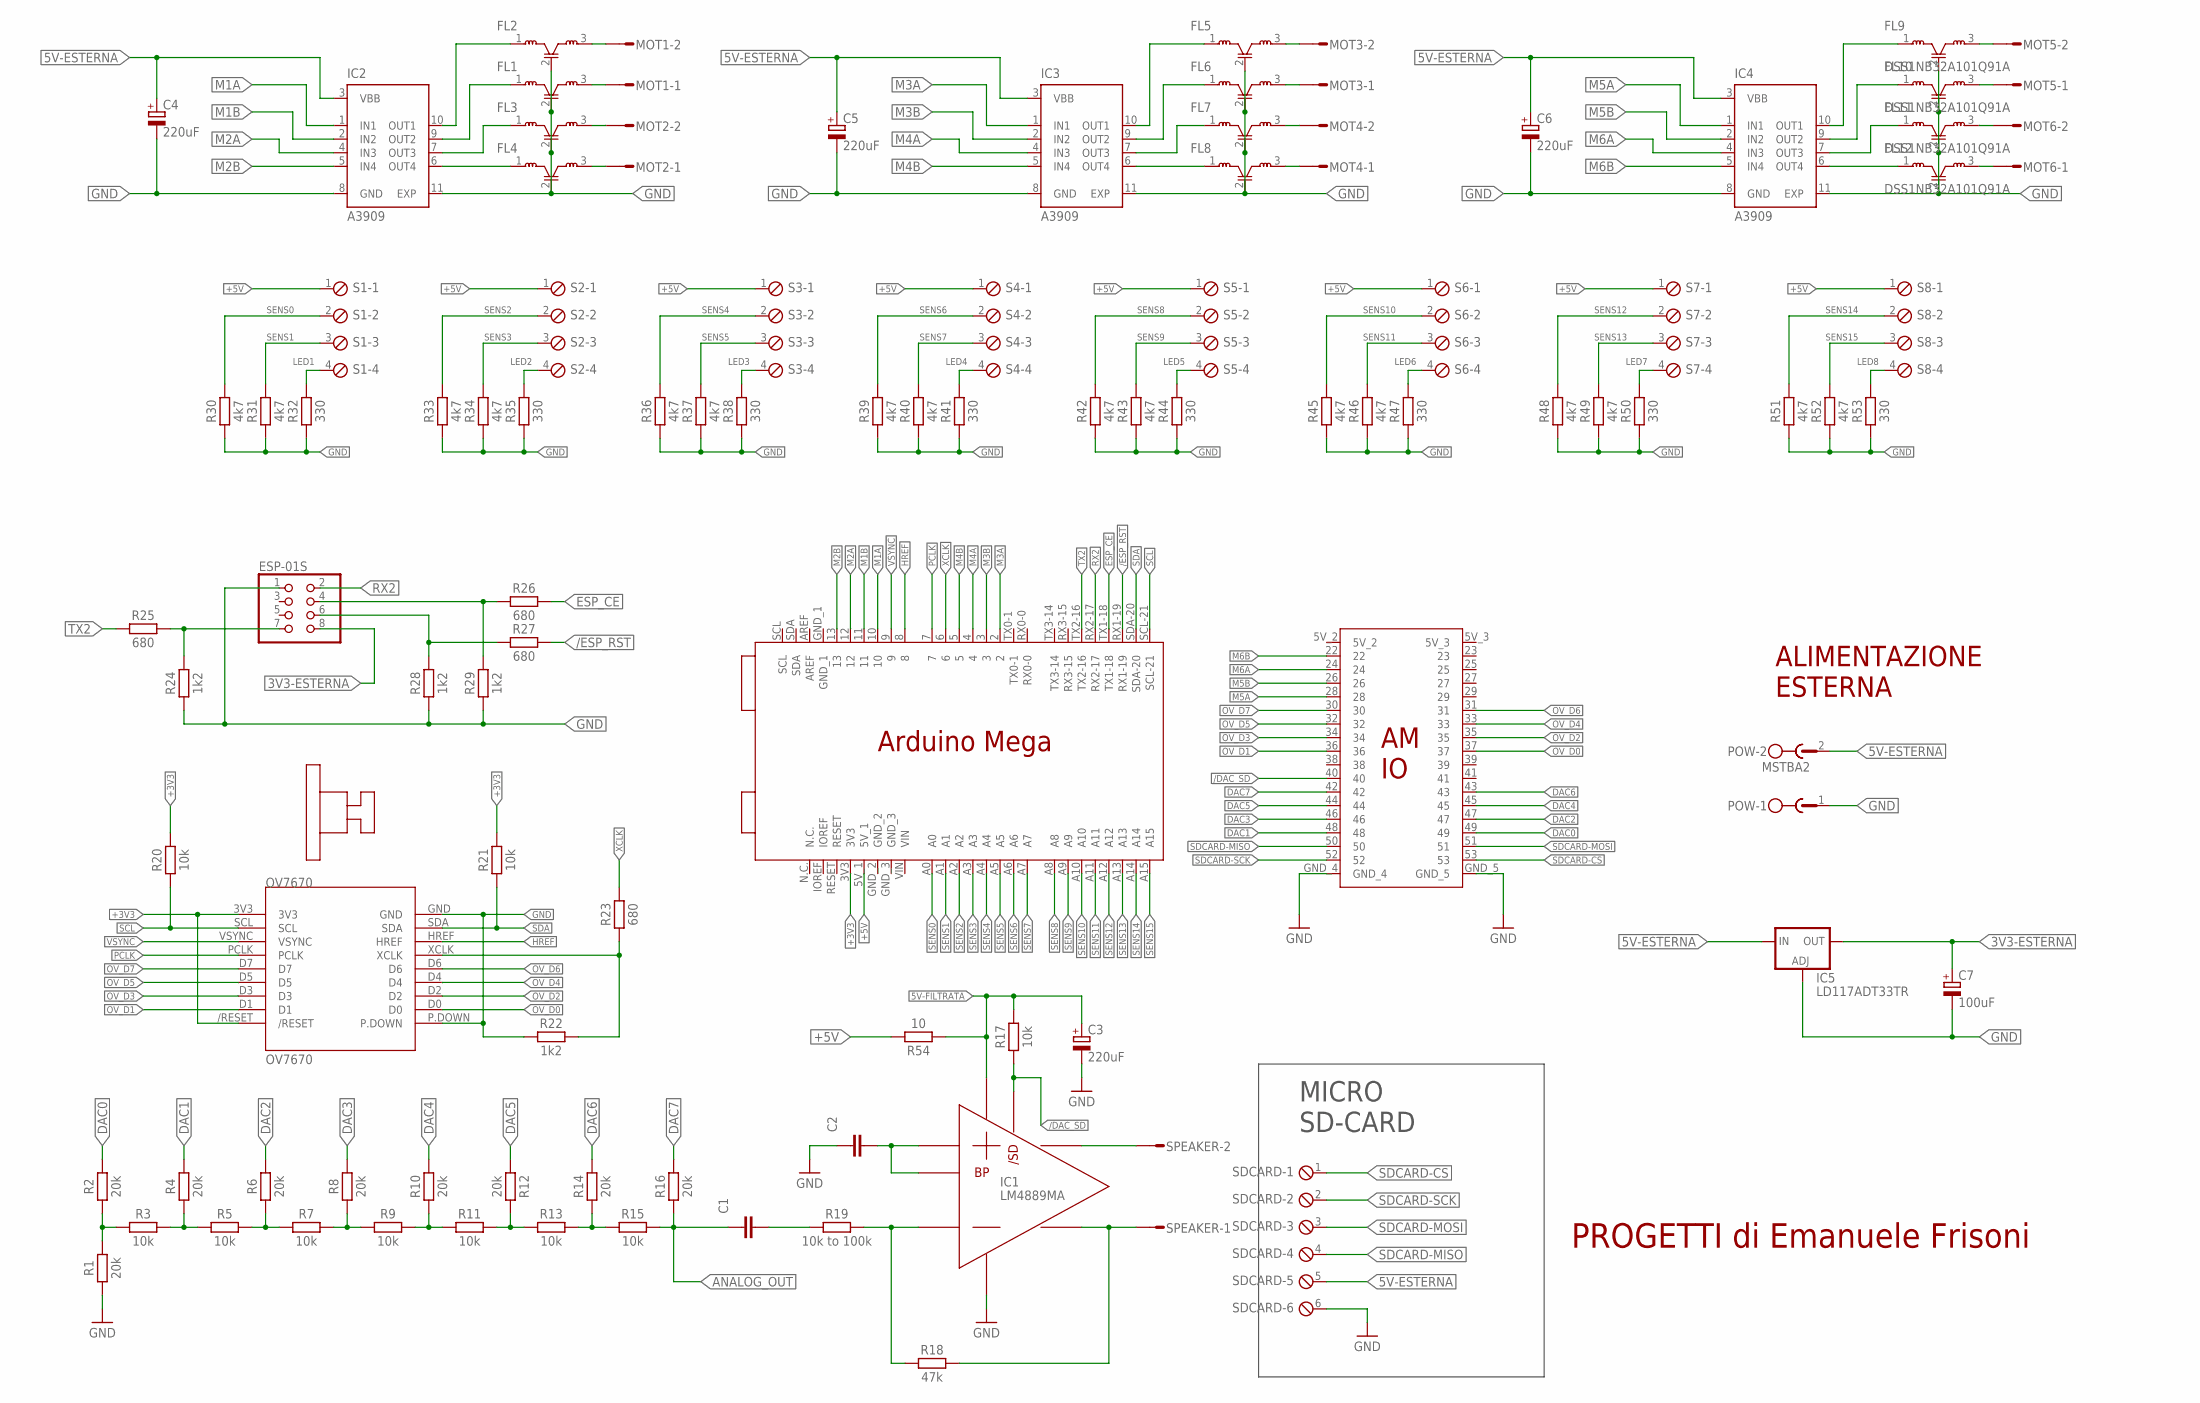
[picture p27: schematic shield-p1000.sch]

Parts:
ARDUINO-MEGA1: ARDUINO-MEGA-SH
C1, C2: 1uF; CAPC1608X85
C3, C4, C5, C6: 220uF; E3,5-10
C7: 100uF; E3,5-10
ESP-01S: PINHD-2X4; 2X04
FL1, FL2, FL3, FL4, FL5, FL6, FL7, FL8, FL9, FL10, FL11, FL12: DSS1NB32A101Q91A; RADIAL-3
IC1: LM4889MA; SOIC127P599X175-8N
IC2, IC3, IC4: A3909; 10-MSOP
IC5: LD117ADT33TR; DPACK
MOT1, MOT2, MOT3, MOT4, MOT5, MOT6: S02P
OV7670: OV7670; OV7670-HEADER
POW: MSTBA2
R1, R2, R4, R6, R8, R10, R12, R14, R16: 20k; RESC1608X60
R3, R5, R7, R9, R11, R13, R15, R17, R20, R21: 10k; RESC1608X60
R18: 47k; RESC1608X60
R19: 10k to 100k; RESAD724W46L381D178B
R22, R24, R28, R29: 1k2; RESC1608X60
R23, R25, R26, R27: 680; RESC1608X60
R30, R31, R33, R34, R36, R37, R39, R40, R42, R43, R45, R46, R48, R49, R51, R52: 4k7; RESC1608X60
R32, R35, R38, R41, R44, R47, R50, R53: 330; RESC1608X60
R54: 10; RESC1608X60
S1, S2, S3, S4, S5, S6, S7, S8: MPT4; 4POL254
SDCARD: MPT6; 6POL254
SPEAKER: S02P

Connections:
3V3-ESTERNA: C7.+, ESP-01S.8, IC5.4 (OUT)
5V-ESTERNA: C4.+, C5.+, C6.+, IC2.3 (VBB), IC3.3 (VBB), IC4.3 (VBB), IC5.3 (IN), POW.2, SDCARD.5
5V-FILTRATA: C3.+, IC1.6 (VDD), R17.1, R54.2
+3V3: ARDUINO-MEGA1.3V3, OV7670.3V3, OV7670./RESET, R20.2, R21.2
+5V: ARDUINO-MEGA1.5V_1, R54.1, S1.1, S2.1, S3.1, S4.1, S5.1, S6.1, S7.1, S8.1
/DAC_SD: ARDUINO-MEGA1.40, IC1.1 (/SHUTDOWN), R17.2
/ESP_RST: ARDUINO-MEGA1.RX1-19, R27.2
ANALOG_OUT: C1.1, R15.1, R16.2
DAC0: ARDUINO-MEGA1.49, R2.1
DAC1: ARDUINO-MEGA1.48, R4.1
DAC2: ARDUINO-MEGA1.47, R6.1
DAC3: ARDUINO-MEGA1.46, R8.1
DAC4: ARDUINO-MEGA1.45, R10.1
DAC5: ARDUINO-MEGA1.44, R12.1
DAC6: ARDUINO-MEGA1.43, R14.1
DAC7: ARDUINO-MEGA1.42, R16.1
ESP_CE: ARDUINO-MEGA1.TX1-18, R26.2
GND: ARDUINO-MEGA1.GND_4, ARDUINO-MEGA1.GND_5, C2.1, C3.-, C4.-, C5.-, C6.-, C7.-, ESP-01S.1, FL1.2 (GND), FL2.2 (GND), FL3.2 (GND), FL4.2 (GND), FL5.2 (GND), FL6.2 (GND), FL7.2 (GND), FL8.2 (GND), FL9.2 (GND), FL10.2 (GND), FL11.2 (GND), FL12.2 (GND), IC1.7 (VSS), IC2.8 (GND), IC2.11 (EXP), IC3.8 (GND), IC3.11 (EXP), IC4.8 (GND), IC4.11 (EXP), IC5.1 (ADJ), OV7670.GND, OV7670.P.DOWN, POW.1, R1.1, R22.1, R24.1, R28.1, R29.1, R30.1, R31.1, R32.1, R33.1, R34.1, R35.1, R36.1, R37.1, R38.1, R39.1, R40.1, R41.1, R42.1, R43.1, R44.1, R45.1, R46.1, R47.1, R48.1, R49.1, R50.1, R51.1, R52.1, R53.1, SDCARD.6
HREF: ARDUINO-MEGA1.8, OV7670.HREF
LED1: R32.2, S1.4
LED2: R35.2, S2.4
LED3: R38.2, S3.4
LED4: R41.2, S4.4
LED5: R44.2, S5.4
LED6: R47.2, S6.4
LED7: R50.2, S7.4
LED8: R53.2, S8.4
M1A: ARDUINO-MEGA1.10, IC2.1 (IN1)
M1B: ARDUINO-MEGA1.11, IC2.2 (IN2)
M2A: ARDUINO-MEGA1.12, IC2.4 (IN3)
M2B: ARDUINO-MEGA1.13, IC2.5 (IN4)
M3A: ARDUINO-MEGA1.2, IC3.1 (IN1)
M3B: ARDUINO-MEGA1.3, IC3.2 (IN2)
M4A: ARDUINO-MEGA1.4, IC3.4 (IN3)
M4B: ARDUINO-MEGA1.5, IC3.5 (IN4)
M5A: ARDUINO-MEGA1.28, IC4.1 (IN1)
M5B: ARDUINO-MEGA1.26, IC4.2 (IN2)
M6A: ARDUINO-MEGA1.24, IC4.4 (IN3)
M6B: ARDUINO-MEGA1.22, IC4.5 (IN4)
unnamed: R1.2, R2.2, R3.2
unnamed: R3.1, R4.2, R5.2
unnamed: R5.1, R6.2, R7.2
unnamed: R7.1, R8.2, R9.2
unnamed: R9.1, R10.2, R11.2
unnamed: R11.1, R12.2, R13.2
unnamed: R13.1, R14.2, R15.2
unnamed: IC1.8 (VO2), SPEAKER.2
unnamed: FL4.1, IC2.6 (OUT4)
unnamed: C1.2, R19.1
unnamed: IC1.4 (IN-), R18.2, R19.2
unnamed: IC1.5 (VO1), R18.1, SPEAKER.1
unnamed: C2.2, IC1.2 (BYPASS), IC1.3 (IN+)
unnamed: ESP-01S.7, R24.2, R25.2
unnamed: ESP-01S.4, R26.1, R29.2
unnamed: ESP-01S.6, R27.1, R28.2
unnamed: FL3.1, IC2.7 (OUT3)
unnamed: FL1.1, IC2.9 (OUT2)
unnamed: FL2.1, IC2.10 (OUT1)
unnamed: FL2.3, MOT1.2
unnamed: FL1.3, MOT1.1
unnamed: FL3.3, MOT2.2
unnamed: FL4.3, MOT2.1
unnamed: FL8.1, IC3.6 (OUT4)
unnamed: FL7.1, IC3.7 (OUT3)
unnamed: FL6.1, IC3.9 (OUT2)
unnamed: FL5.1, IC3.10 (OUT1)
unnamed: FL5.3, MOT3.2
unnamed: FL6.3, MOT3.1
unnamed: FL7.3, MOT4.2
unnamed: FL8.3, MOT4.1
unnamed: FL12.1, IC4.6 (OUT4)
unnamed: FL11.1, IC4.7 (OUT3)
unnamed: FL10.1, IC4.9 (OUT2)
unnamed: FL9.1, IC4.10 (OUT1)
unnamed: FL9.3, MOT5.2
unnamed: FL10.3, MOT5.1
unnamed: FL11.3, MOT6.2
unnamed: FL12.3, MOT6.1
OV_D0: ARDUINO-MEGA1.37, OV7670.D0
OV_D1: ARDUINO-MEGA1.36, OV7670.D1
OV_D2: ARDUINO-MEGA1.35, OV7670.D2
OV_D3: ARDUINO-MEGA1.34, OV7670.D3
OV_D4: ARDUINO-MEGA1.33, OV7670.D4
OV_D5: ARDUINO-MEGA1.32, OV7670.D5
OV_D6: ARDUINO-MEGA1.31, OV7670.D6
OV_D7: ARDUINO-MEGA1.30, OV7670.D7
PCLK: ARDUINO-MEGA1.7, OV7670.PCLK
RX2: ARDUINO-MEGA1.RX2-17, ESP-01S.2
SCL: ARDUINO-MEGA1.SCL-21, OV7670.SCL, R20.1
SDA: ARDUINO-MEGA1.SDA-20, OV7670.SDA, R21.1
SDCARD-CS: ARDUINO-MEGA1.53, SDCARD.1
SDCARD-MISO: ARDUINO-MEGA1.50, SDCARD.4
SDCARD-MOSI: ARDUINO-MEGA1.51, SDCARD.3
SDCARD-SCK: ARDUINO-MEGA1.52, SDCARD.2
SENS0: ARDUINO-MEGA1.A0, R30.2, S1.2
SENS1: ARDUINO-MEGA1.A1, R31.2, S1.3
SENS2: ARDUINO-MEGA1.A2, R33.2, S2.2
SENS3: ARDUINO-MEGA1.A3, R34.2, S2.3
SENS4: ARDUINO-MEGA1.A4, R36.2, S3.2
SENS5: ARDUINO-MEGA1.A5, R37.2, S3.3
SENS6: ARDUINO-MEGA1.A6, R39.2, S4.2
SENS7: ARDUINO-MEGA1.A7, R40.2, S4.3
SENS8: ARDUINO-MEGA1.A8, R42.2, S5.2
SENS9: ARDUINO-MEGA1.A9, R43.2, S5.3
SENS10: ARDUINO-MEGA1.A10, R45.2, S6.2
SENS11: ARDUINO-MEGA1.A11, R46.2, S6.3
SENS12: ARDUINO-MEGA1.A12, R48.2, S7.2
SENS13: ARDUINO-MEGA1.A13, R49.2, S7.3
SENS14: ARDUINO-MEGA1.A14, R51.2, S8.2
SENS15: ARDUINO-MEGA1.A15, R52.2, S8.3
TX2: ARDUINO-MEGA1.TX2-16, R25.1
VSYNC: ARDUINO-MEGA1.9, OV7670.VSYNC
XCLK: ARDUINO-MEGA1.6, R23.2
XCLK1: OV7670.XCLK, R22.2, R23.1

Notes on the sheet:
MICRO SD-CARD
ALIMENTAZIONE ESTERNA
PROGETTI di Emanuele Frisoni

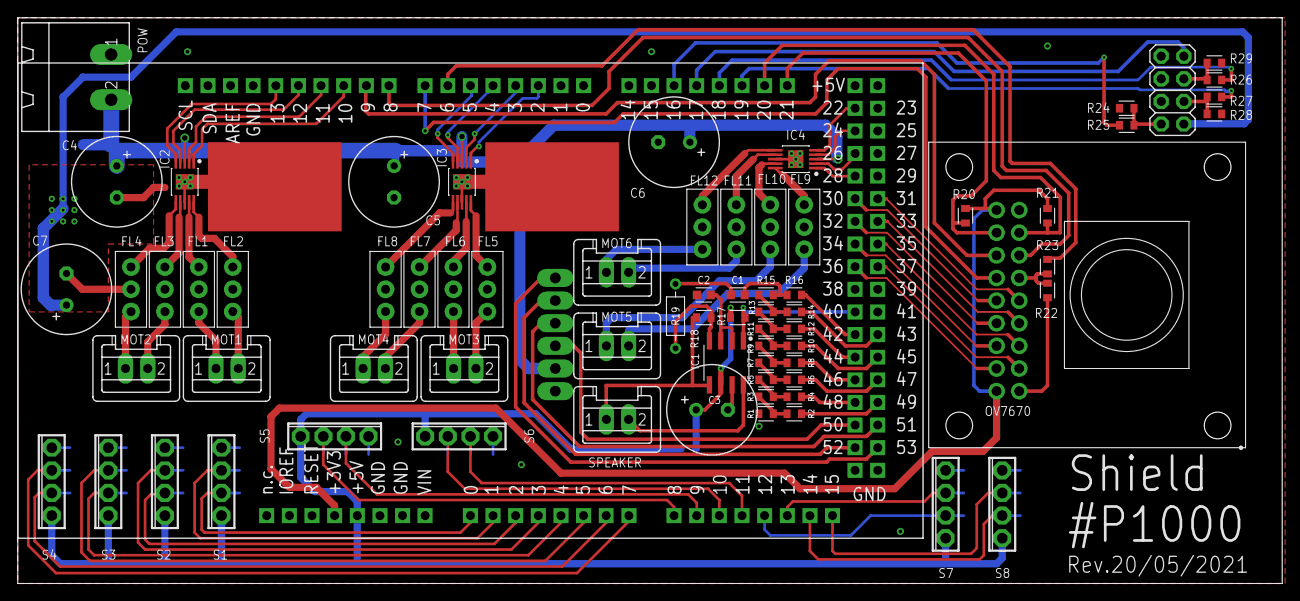
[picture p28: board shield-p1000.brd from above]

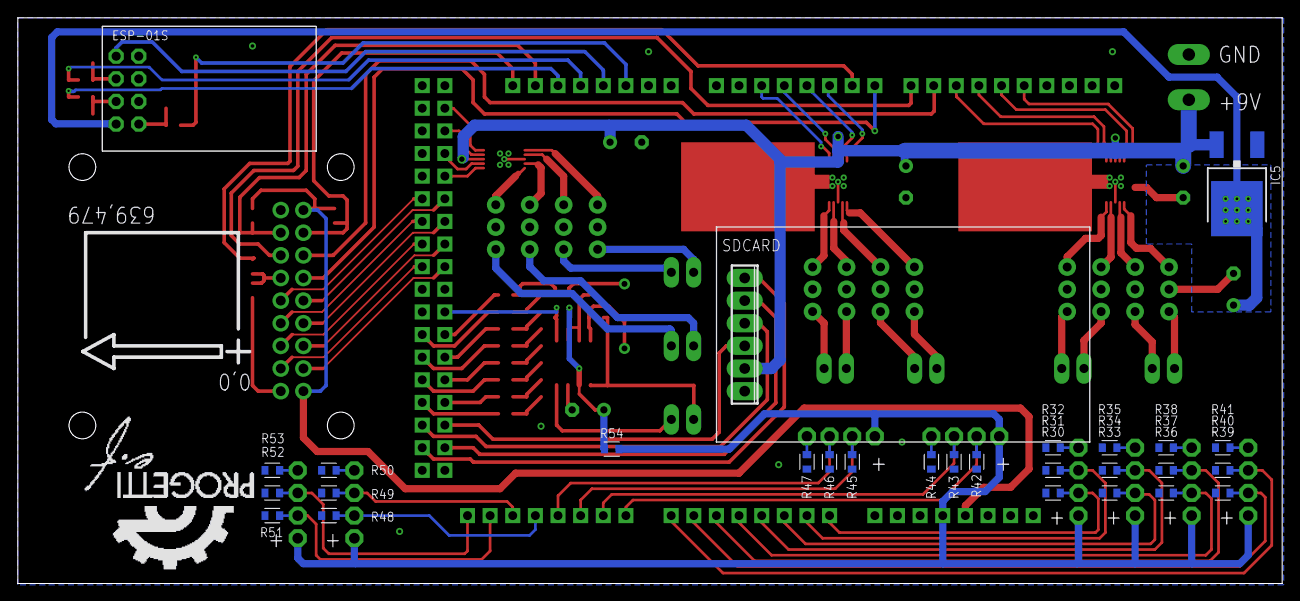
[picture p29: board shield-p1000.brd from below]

Board: 2 copper layers, 141.9 x 63.5 mm, 98 parts (27 on the bottom side), 114 nets.

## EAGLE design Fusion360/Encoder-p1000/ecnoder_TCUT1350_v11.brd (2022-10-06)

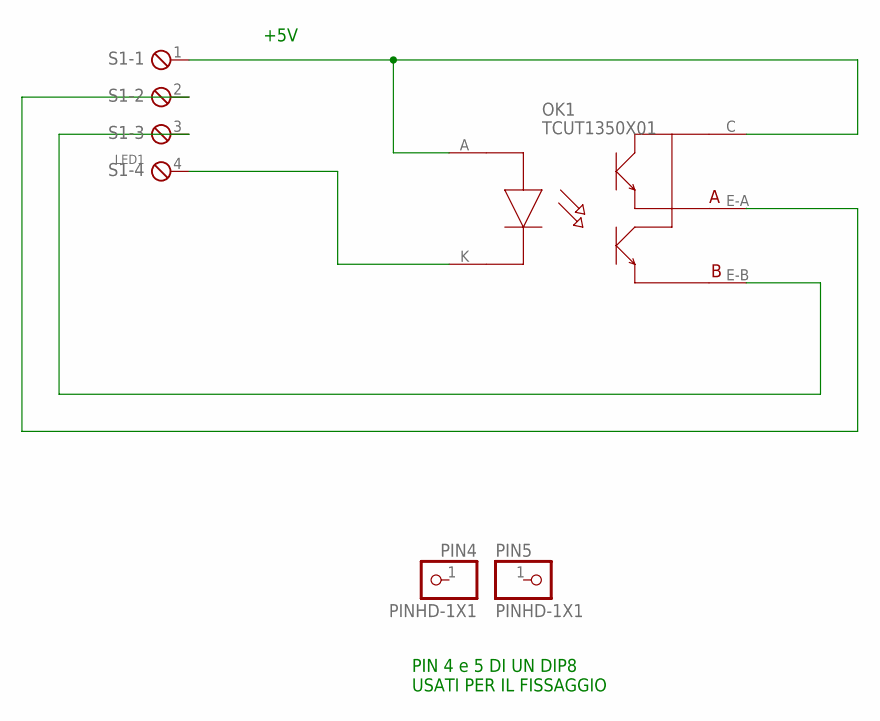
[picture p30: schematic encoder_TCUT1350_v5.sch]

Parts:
OK1: TCUT1350X01
PIN4, PIN5: PINHD-1X1; 1X01
S1: MPT4; 4POL254

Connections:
+5V: OK1.A, OK1.C, S1.1
LED1: OK1.K, S1.4
unnamed: OK1.E-B, S1.3
unnamed: OK1.E-A, S1.2

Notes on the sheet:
+5V
PIN 4 e 5 DI UN DIP8 USATI PER IL FISSAGGIO

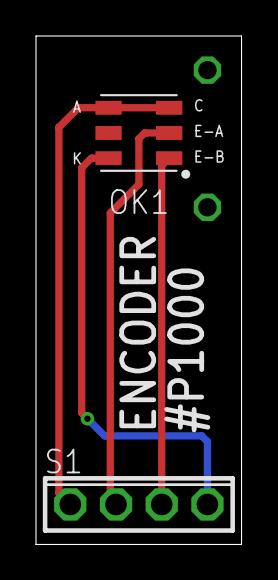
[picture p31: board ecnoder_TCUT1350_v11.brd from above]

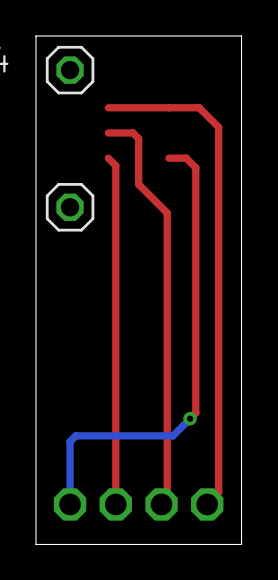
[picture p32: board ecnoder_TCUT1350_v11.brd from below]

Board: 2 copper layers, 11.4 x 28.2 mm, 4 parts (2 on the bottom side), 4 nets.

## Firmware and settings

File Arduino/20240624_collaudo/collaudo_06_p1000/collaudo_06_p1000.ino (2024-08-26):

/*
  Collaudo del Robot P1000.

  Questo programma serve a collaudare tutte le funzionalità
  del robot P1000, una alla volta:

  * collaudo della SD-Card e DAC (sdcard.ino)
  * collaudo motori
  * collaudo sensori angolari dei polsi
  * collaudo encoder apertura delle mani
  * all'accensione la mano DX, poi apre la mano SX  
  * gestione dei sensori degli encoder a interrupt
    con https://github.com/NicoHood/PinChangeInterrupt v1.2.9
  
  https://www.youtube.com/live/M33s9mqJizs
  
  Bologna, 26 agosto 2024
*/

#include "defs.h"

enum STATI_MACCHINA {
  ST_RESET = 0,
  ST_CERCA_APERTURA_MANO_DX,
  ST_MANO_DX_APERTA,
  ST_CERCA_APERTURA_MANO_SX,
  ST_MANO_SX_APERTA,
  ST_APRI_CHIUDI
} stato_macchina;

void setup() {

  // SERIALE DI SERVIZIO PER DEBUG
  Serial.begin(115200);

  while (!Serial) {
    /* wait for serial port to connect. Needed for native USB port only */
    /* do nothing */;
  }

  setup_motori();
  setup_joystick();
  setup_sensori_angolari();
  setup_sensori_presa();

  setup_sdcard();

  //play_something( "audio/track001.raw" );
  //play_something( "audio/track002.raw" );

  stato_macchina = ST_RESET;
}

int regime = 0;

void loop() {
  char s[100];
  int stato;
  unsigned long t;

/*
sprintf(s, "JOY-SX x:%d\ty:%d\tJOY-DX x:%d\ty:%d"
           , getJoystickSxX()
           , getJoystickSxY()
           , getJoystickDxX()
           , getJoystickDxY() );         
*/
/*
sprintf(s, "A4:%d,A2:%d,A5:%d,A1:%d,A3:%d,A0:%d"
           , analogRead(A4)
           , analogRead(A2)
           , analogRead(A5)
           , analogRead(A1)
           , analogRead(A3)
           , analogRead(A0) );
*/
  /*
sprintf(s, "SENS-SX:%d  SENS-DX:%d "
           , getRotazionePolsoSX()
           , getRotazionePolsoDX() );
*/
  /*
sprintf(s, "A8:%d,A9:%d,A10:%d,A11:%d"
           , digitalRead(A8)
           , digitalRead(A9)
           , digitalRead(A10)
           , digitalRead(A11) );
*/

sprintf(s, "DX=%d; SX=%d, r=%d, s=%d"
           , get_corsa_mano_DX()
           , get_corsa_mano_SX()
           , regime, stato_macchina
          );
  Serial.println(s);


  switch (stato_macchina) {

    case ST_RESET:
      setSpeedMotoreDxPresa(500);
      regime = 0;
      stato = get_corsa_mano_DX(); 
      delay(100);
      stato_macchina = ST_CERCA_APERTURA_MANO_DX;
      break;

    case ST_CERCA_APERTURA_MANO_DX:
      if (regime == 0) {
        if (deltaT_encoder_presa_mano_DX() < DELTA_T_BUCO_ENCODER) {
          //ogni volta che c'è un cambio di stato nell'encoder
          regime=1;
          stato = get_corsa_mano_DX();
        }
      } else {
        t = deltaT_encoder_presa_mano_DX();  // si aggiorna ad interrupt
        if (t > DELTA_T_BUCO_ENCODER) {
          // la mano DX ora è aperta
          setSpeedMotoreDxPresa(0);
          stato_macchina = ST_MANO_DX_APERTA;
        }
      }
      break;

    case ST_MANO_DX_APERTA:
      setSpeedMotoreSxPresa(-500);
      regime = 0;
      stato = get_corsa_mano_SX();
      delay(1000);
      stato_macchina = ST_CERCA_APERTURA_MANO_SX;
      break;

    case ST_CERCA_APERTURA_MANO_SX:
      if (regime == 0) {
        if (deltaT_encoder_presa_mano_SX() < DELTA_T_BUCO_ENCODER) {
          //ogni volta che c'è un cambio di stato nell'encoder
          regime = 1;
          stato = get_corsa_mano_SX();
        }
      } else {
        t = deltaT_encoder_presa_mano_SX();  // si aggiorna ad interrupt
        if (t > DELTA_T_BUCO_ENCODER) {
          // la mano SX ora è aperta
          setSpeedMotoreSxPresa(0);
          stato_macchina = ST_MANO_SX_APERTA;
        }
      }

    case ST_MANO_SX_APERTA:
      /* do something more */
      setSpeedMotoreDxPresa(0);
      setSpeedMotoreSxPresa(0);
      delay(100);
      azzera_corsa_mano_DX();
      azzera_corsa_mano_SX();
      
      /* posizione di partenza */
      setSpeedMotoreDxRotazione(  300 );
      setSpeedMotoreSxRotazione( -300 );
      while (getRotazionePolsoSX() != DITO_CENTRALE_ALTO) /* do nothing */;
      setSpeedMotoreSxRotazione( 0 );
      while (getRotazionePolsoDX() != DITO_CENTRALE_BASSO) /* do nothing */;
      setSpeedMotoreDxRotazione( 0 );
      
      stato_macchina = ST_APRI_CHIUDI;
      break;

    case ST_APRI_CHIUDI:
      if (joystickDxPressed()) {
        // apri e chiudi mano DX
        if (get_corsa_mano_DX() <= 0) {
          // la mano è aperta
          // la chiudiamo per afferrare il cubo
          setSpeedMotoreDxPresa(FORZA_CHIUSURA_MANO_DX);
          while (get_corsa_mano_DX() <= 0) /* wait */;
          do {
            t = deltaT_encoder_presa_mano_DX();  // si aggiorna ad interrupt
          } while (t < DELTA_T_BUCO_ENCODER);
          // la mano ha afferrato qualcosa (o è arrivata al buco)
          setSpeedMotoreDxPresa(FORZA_MANTENIMENTO_CHIUSURA_MANO_DX);   
        }
        else {
          // la mano sta afferrrando il cubo
          // la apriamo per mollare il cubo
          stato = get_corsa_mano_DX();
          setSpeedMotoreDxPresa(FORZA_APERTURA_MANO_DX);
          while (get_corsa_mano_DX() == stato) /* wait */;
          do {
            t = deltaT_encoder_presa_mano_DX();  // si aggiorna ad interrupt
          } while (t < DELTA_T_BUCO_ENCODER);
          // la mano ha afferrato qualcosa (o è arrivata al buco)
          setSpeedMotoreDxPresa(0);   
        }
      }

      if (joystickSxPressed()) {
        // apri e chiudi mano SX
        if (get_corsa_mano_SX() <= 0) {
          // la mano è aperta
          // la chiudiamo per afferrare il cubo
          setSpeedMotoreSxPresa(FORZA_CHIUSURA_MANO_SX);
          while (get_corsa_mano_SX() <= 0) /* wait */;
          do {
            t = deltaT_encoder_presa_mano_SX();  // si aggiorna ad interrupt
          } while (t < DELTA_T_BUCO_ENCODER);
          // la mano ha afferrato qualcosa (o è arrivata al buco)
          setSpeedMotoreSxPresa(FORZA_MANTENIMENTO_CHIUSURA_MANO_SX);   
        }
        else {
          // la mano sta afferrrando il cubo
          // la apriamo per mollare il cubo
          stato = get_corsa_mano_SX();
          setSpeedMotoreSxPresa(FORZA_APERTURA_MANO_SX);
          while (get_corsa_mano_SX() == stato) /* wait */;
          do {
            t = deltaT_encoder_presa_mano_SX();  // si aggiorna ad interrupt
          } while (t < DELTA_T_BUCO_ENCODER);
          // la mano ha afferrato qualcosa (o è arrivata al buco)
          setSpeedMotoreSxPresa(0);   
        }
      }

      if (getJoystickDxX() > 500) {
        ruotaManoDx(DITO_CENTRALE_LONTANO);
      } else if (getJoystickDxX() < -500) {
        ruotaManoDx(DITO_CENTRALE_VICINO);
      } else if (getJoystickDxY() > 500) {
        ruotaManoDx(DITO_CENTRALE_ALTO);
      } else if (getJoystickDxY() < -500) {
        ruotaManoDx(DITO_CENTRALE_BASSO);
      }

      if (getJoystickSxX() < -500) {
        ruotaManoSx(DITO_CENTRALE_LONTANO);
      } else if (getJoystickSxX() > 500) {
        ruotaManoSx(DITO_CENTRALE_VICINO);
      } else if (getJoystickSxY() > 500) {
        ruotaManoSx(DITO_CENTRALE_ALTO);
      } else if (getJoystickSxY() < -500) {
        ruotaManoSx(DITO_CENTRALE_BASSO);
      }
      break;

    default:
      /*
      if (getJoystickDxX() > 500) {
        ruotaManoDx(DITO_CENTRALE_LONTANO);
      } else if (getJoystickDxX() < -500) {
        ruotaManoDx(DITO_CENTRALE_VICINO);
      } else if (getJoystickDxY() > 500) {
        ruotaManoDx(DITO_CENTRALE_ALTO);
      } else if (getJoystickDxY() < -500) {
        ruotaManoDx(DITO_CENTRALE_BASSO);
      }

      if (getJoystickSxX() < -500) {
        ruotaManoSx(DITO_CENTRALE_LONTANO);
      } else if (getJoystickSxX() > 500) {
        ruotaManoSx(DITO_CENTRALE_VICINO);
      } else if (getJoystickSxY() > 500) {
        ruotaManoSx(DITO_CENTRALE_ALTO);
      } else if (getJoystickSxY() < -500) {
        ruotaManoSx(DITO_CENTRALE_BASSO);
      }
      */
      break;
  }
}

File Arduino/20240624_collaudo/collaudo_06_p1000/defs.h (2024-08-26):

/* sensori angolari */

#define SOGLIA_DI_LUCE_FINESTRELLA_H  150
#define SOGLIA_DI_LUCE_FINESTRELLA_L   50

#define DELTA_T_BUCO_ENCODER           50L /* millisecondi */
#define MAX_CONTEGGIO_ENCODER          64  /* 20 denti = 20x4=80 */

#define SENSORE_1_MANO_DX           A1
#define SENSORE_2_MANO_DX           A3
#define SENSORE_3_MANO_DX           A0

#define SENSORE_1_MANO_SX           A4
#define SENSORE_2_MANO_SX           A2
#define SENSORE_3_MANO_SX           A5

#define SENSORE_A_MANO_DX           62  //A8
#define SENSORE_B_MANO_DX           63  //A9

#define SENSORE_A_MANO_SX           64  //A10
#define SENSORE_B_MANO_SX           65  //A11

#define DITO_CENTRALE_LONTANO        3
#define DITO_CENTRALE_VICINO         6
#define DITO_CENTRALE_BASSO          2
#define DITO_CENTRALE_ALTO           7

/* MOTORI MANO DX */
#define MOT1A 10
#define MOT1B 11
#define MOT2A 12
#define MOT2B 23    // in origine era 13

/* MOTORI MANO SX */
#define MOT3A 2
#define MOT3B 3
#define MOT4A 4
#define MOT4B 5

#define FORZA_APERTURA_MANO_DX   500
#define FORZA_CHIUSURA_MANO_DX   -800
#define FORZA_MANTENIMENTO_CHIUSURA_MANO_DX  -100
#define FORZA_ROTAZIONE_MANO_DX  750

#define FORZA_APERTURA_MANO_SX   -500
#define FORZA_CHIUSURA_MANO_SX   800
#define FORZA_MANTENIMENTO_CHIUSURA_MANO_SX  100
#define FORZA_ROTAZIONE_MANO_SX  750

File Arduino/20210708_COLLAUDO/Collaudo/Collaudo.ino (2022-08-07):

/*
  SD card file dump

  This example shows how to read a file from the SD card using the
  SD library and send it over the serial port.

  The circuit:
   SD card attached to SPI bus as follows:
 ** MOSI - pin 11 (UNO) / 51 (MEGA)
 ** MISO - pin 12 (UNO) / 50 (MEGA)
 ** CLK -  pin 13 (UNO) / 52 (MEGA)
 ** CS -   pin 10 (UNO) / 53 (MEGA)  [(for MKRZero SD: SDCARD_SS_PIN)]

  Appunti:
 ** https://www.arduino.cc/en/Hacking/PinMapping2560
 ** https://www.arduino.cc/en/reference/SPI
 ** https://www.arduino.cc/en/reference/SD
   
  created  22 December 2010
  by Limor Fried
  modified 9 Apr 2012
  by Tom Igoe

  riadattato il 17 Dicembre 2020
  per Progetto1000 da Emanuele Frisoni
  
  Guarda il video: https://www.youtube.com/watch?v=kRmUnPmCAZg

  This example code is in the public domain.
*/

#include <SPI.h>
#include <SD.h>

#define  DEBUG_PIN             8

#define  CSPIN                53    /* per Arduino Mega il default è 53 */
#define  DAC_SHUT_DOWN        40
#define  NOMEFILE  "datalog.txt"

#define  MOT1A                10
#define  MOT1B                11
#define  MOT2A                12
#define  MOT2B                13

#define  MOT3A                2
#define  MOT3B                3
#define  MOT4A                4
#define  MOT4B                5

#define  MOT5A                28
#define  MOT5B                26
#define  MOT6A                24
#define  MOT6B                22

#define  SENS0                A0
#define  SENS1                A1
#define  SENS2                A2
#define  SENS3                A3
#define  SENS4                A4
#define  SENS5                A5
#define  SENS6                A6
#define  SENS7                A7
#define  SENS8                A8
#define  SENS9                A9
#define  SENS10               A10
#define  SENS11               A11
#define  SENS12               A12
#define  SENS13               A13
#define  SENS14               A14
#define  SENS15               A15


volatile signed int vel_mot1;       /* velocita va da -100 a +100 */


#define SIZE_CIRCULAR_BUFFER 64
#define MASK_CIRCULAR_BUFFER 0x3F

volatile unsigned char circular_buffer[ SIZE_CIRCULAR_BUFFER ];
volatile unsigned char circular_buffer_head, circular_buffer_tail, circular_buffer_len;

void mio_delay(int msec);
void play_something(char * nomefile);


void setup() {
  /* Open serial communications and wait for port to open: */
  Serial.begin(115200);
  
  while (!Serial) {
    /* wait for serial port to connect. Needed for native USB port only */
    /* do nothing */;    
  }

#if FALSE
  Serial.print("Initializing SD card...");

  // see if the card is present and can be initialized:
  if (!SD.begin(CSPIN)) {
    
    Serial.println("Card failed, or not present");
    while (1); 
    
  }
  
  Serial.println("card initialized.");
#endif

  /* inizializzazione buffer circolare */
  circular_buffer_head = 0;
  circular_buffer_tail = 0;
  circular_buffer_len  = 0;

  /* impostazione Timer 3 per dare 
   * un interrupt a 8ksps ogni 125 uSec
   * Quarzo = 16MHz; 62,5 nSec ---> 2000 impulsi ogni 125 uSec
   */
  cli();
  TCCR5A = 0x00;
  // prescaler 
  TCCR5B = 0x01;    /* modalità Clear Timer on Compare Match e senza prescaler */
  // conteggio da raggiungere
  OCR5A = (2000 - 1);
  // attivo CTC Mode
  TCCR5B |= 0x08;
  // abilita interrupt on match counter
  TIMSK5 = 0x02;
  sei();

  pinMode(DAC_SHUT_DOWN, OUTPUT); /* ABILITAZIONE AMPLIFICATORE ATTIVO BASSO */ 
  digitalWrite( DAC_SHUT_DOWN, LOW );
  
  /* PORT-L PINS per DAC */
  pinMode(42, OUTPUT); /* PORT - L7 - Most Significant bit */ 
  pinMode(43, OUTPUT);
  pinMode(44, OUTPUT);
  pinMode(45, OUTPUT);
  pinMode(46, OUTPUT);
  pinMode(47, OUTPUT);
  pinMode(48, OUTPUT);
  pinMode(49, OUTPUT); /* PORT - L0 - Least Significant bit*/ 
  PORTL = 128;
   

#ifdef DEBUG_MODE 
  pinMode( DEBUG_PIN , OUTPUT); 
#endif

  //play_something( "audio/track001.raw" );
  //play_something( "audio/track002.raw" );

  pinMode(MOT1A, OUTPUT); 
  pinMode(MOT1B, OUTPUT); 
  digitalWrite( MOT1A, HIGH );
  digitalWrite( MOT1B, HIGH );
  vel_mot1 = 50;
  
}

void loop() {

  static unsigned long t1 = millis(), t2;
  static int inversione = 1;
  static int passi = 0, stato = 0;

  /*
   
   Serial.print ( "0," );
   Serial.print ( analogRead( SENS0 ) );
   Serial.print ( "," );
   Serial.println ( analogRead( SENS1 ) );
  
  */

  /*
   CALCOLO RPM
   
  while ( digitalRead(SENS15) == 0 ) /* do nothing * /;

  t2 = 60000000UL / (micros() - t1);
  t1 = micros();

  while ( digitalRead(SENS15) == 1 ) /* do nothing * /;

  Serial.println ( t2 );
  */

  /* 
   *  CONTEGGIO PASSI
   *  
   */
   switch( stato )
   {

//  stato   0   1   2   3   0 
//   14     0   1   1   0   0
//   15     0   0   1   1   0

    case 0: 
      if ( digitalRead(SENS14) == 1) { stato = 1; }
      if ( digitalRead(SENS15) == 1) { stato = 3; }
      break;    
       
    case 1: 
      if ( digitalRead(SENS14) == 0) { stato = 0; passi --; }
      if ( digitalRead(SENS15) == 1) { stato = 2; }
      break;    
    
    case 2: 
      if ( digitalRead(SENS14) == 0) { stato = 3; }
      if ( digitalRead(SENS15) == 0) { stato = 1; }
      break;    

    case 3: 
      if ( digitalRead(SENS14) == 1) { stato = 2; }
      if ( digitalRead(SENS15) == 0) { stato = 0; passi++; }
      break;    
    
   }

   t2 = (millis() - t1);
   if (t2 >= 100) 
   {
     t1 = millis();
     Serial.println ( passi );

     inversione --; 
     if (inversione <= 0) 
     {
       if (vel_mot1 == 50) 
         { vel_mot1 = -50; }
       else 
         { vel_mot1 = 50; }
     
       inversione = 100;
     }
   }

}

void loop1() {

  Serial.println("Motore Avanti");

  vel_mot1 = 30;

  while (vel_mot1 < 80) {
    mio_delay(50);
    vel_mot1 ++;
  }

  mio_delay(2000);

  while (vel_mot1 > 30) {
    mio_delay(50);
    vel_mot1 --;
  }

  vel_mot1 = 0;
  mio_delay(2000);


  Serial.println("Motore Indietro");

  vel_mot1 = -30;

  while (vel_mot1 > -80) {
    mio_delay(50);
    vel_mot1 --;
  }

  mio_delay(2000);

  while (vel_mot1 < -30) {
    mio_delay(50);
    vel_mot1 ++;
  }
  
  vel_mot1 = 0;
  mio_delay(2000);

}

void mio_delay(int msec)
{
  unsigned long t;

  t = millis() + msec;
  while (millis() < t) { /* do_nothing */ } 

}
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

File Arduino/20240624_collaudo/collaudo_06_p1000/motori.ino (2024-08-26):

/*
 * I motori del robot P1000 sono i seguenti:
 * 
 *  * MOT1 ( mano DX 1 ) 10-11
 *  * MOT2 ( mano DX 2 ) 12-23(in origine era 13)
 *  * MOT3 ( mano SX 1 )  2-3
 *  * MOT4 ( mano SX 2 )  4-5
 *  
 */

#include "defs.h"

int angolo_mano_dx, angolo_mano_sx;

void setup_motori() {

  Serial.println("Setup motori");
  analogWrite( MOT1A, 0 ); //pinMode ( MOT1A, OUTPUT ); digitalWrite( MOT1A, LOW );
  analogWrite( MOT1B, 0 ); //pinMode ( MOT1B, OUTPUT ); digitalWrite( MOT1B, LOW );
  analogWrite( MOT2A, 0 );//pinMode ( MOT2A, OUTPUT ); digitalWrite( MOT2A, LOW );
  pinMode ( MOT2B, OUTPUT ); digitalWrite( MOT2B, LOW );
  analogWrite( MOT3A, 0 ); //pinMode ( MOT3A, OUTPUT ); digitalWrite( MOT3A, LOW );
  analogWrite( MOT3B, 0 ); //pinMode ( MOT3B, OUTPUT ); digitalWrite( MOT3B, LOW );
  analogWrite( MOT4A, 0 ); //pinMode ( MOT4A, OUTPUT ); digitalWrite( MOT4A, LOW );
  analogWrite( MOT4B, 0 ); //pinMode ( MOT4B, OUTPUT ); digitalWrite( MOT4B, LOW );
  
  angolo_mano_dx = 0;
  angolo_mano_sx = 0;

}

/* il range di velocità va da -1000 a +1000 */
void setSpeedMotoreDxPresa( int speed1000 ) {

  if (speed1000 > 50) {
    analogWrite( MOT1A, map(speed1000, 0, 1000, 50, 255));
    analogWrite( MOT1B, 0 );
  }
  else if (speed1000 < -50) {
    analogWrite( MOT1A, 0 );
    analogWrite( MOT1B, map(speed1000, 0, -1000, 50, 255));
  }
  else {
    analogWrite( MOT1A, 0 );
    analogWrite( MOT1B, 0 );
  }
}

/* il range di velocità va da -1000 a +1000          */
/* valori positivi devono far girare                 */
/* la faccia del cubo in senso orario                */
void setSpeedMotoreDxRotazione( int speed1000 ) {
  // commentare la definizione sbagliata
  
  //const int m1=MOT2A, m2=MOT2B; 
  const int m1=MOT2B, m2=MOT2A;
  
  if (speed1000 > 50) {
    digitalWrite( m1, 1 ); /* analogWrite( m1, map... ); su pin 23 non c'è PWM */
    analogWrite( m2, 255 - map(speed1000, 0, 1000, 50, 255) ); 
  }
  else if (speed1000 < -50) {
    digitalWrite( m1, 0 ); /* analogWrite( m1, 0 );   su pin 23 non c'è PWM */
    analogWrite( m2, map(speed1000, 0, -1000, 50, 255) ); 
  }
  else {
    digitalWrite( m1, 0 ); /* analogWrite( m2, 0 );  su pin 23 non c'è PWM */
    analogWrite( m2, 0 ); 
  }
}

/* il range di velocità va da -1000 a +1000 */
void setSpeedMotoreSxPresa( int speed1000 ) {

  if (speed1000 > 50) {
    analogWrite( MOT3A, map(speed1000, 0, 1000, 50, 255));
    analogWrite( MOT3B, 0 );
  }
  else if (speed1000 < -50) {
    analogWrite( MOT3A, 0 );
    analogWrite( MOT3B, map(speed1000, 0, -1000, 50, 255));
  }
  else {
    analogWrite( MOT3A, 0 );
    analogWrite( MOT3B, 0 );
  }
}

/* il range di velocità va da -1000 a +1000          */
/* valori positivi devono far girare                 */
/* la faccia del cubo in senso orario                */
void setSpeedMotoreSxRotazione( int speed1000 ) {
  // commentare la definizione sbagliata
  
  //const int m1=MOT4A, m2=MOT4B; 
  const int m1=MOT4B, m2=MOT4A;
  
  if (speed1000 > 50) {
    analogWrite( m1, map(speed1000, 0, 1000, 50, 255));
    analogWrite( m2, 0 );
  }
  else if (speed1000 < -50) {
    analogWrite( m1, 0 );
    analogWrite( m2, map(speed1000, 0, -1000, 50, 255));
  }
  else {
    analogWrite( m1, 0 );
    analogWrite( m2, 0 );
  }
}

void ruotaManoDx(int destinazione) {
  int speed;
  unsigned long t0, t1;
  
  if (angolo_mano_dx != destinazione) {

    if ((angolo_mano_dx == DITO_CENTRALE_ALTO) && (destinazione == DITO_CENTRALE_VICINO)) {
      speed = -FORZA_ROTAZIONE_MANO_DX;
    } else 
    if ((angolo_mano_dx == DITO_CENTRALE_LONTANO) && (destinazione == DITO_CENTRALE_ALTO)) {
      speed = -FORZA_ROTAZIONE_MANO_DX;
    } else 
    if ((angolo_mano_dx == DITO_CENTRALE_BASSO) && (destinazione == DITO_CENTRALE_LONTANO)) {
      speed = -FORZA_ROTAZIONE_MANO_DX;
    } else 
    if ((angolo_mano_dx == DITO_CENTRALE_VICINO) && (destinazione == DITO_CENTRALE_BASSO)) {
      speed = -FORZA_ROTAZIONE_MANO_DX;
    } else {
      speed = FORZA_ROTAZIONE_MANO_DX;
    }
    setSpeedMotoreDxRotazione( speed );

    while (getRotazionePolsoDX() != 0) /* do nothing */;
    delay(50);

    while (getRotazionePolsoDX() != destinazione) /* do nothing */;
    t0 = millis();
    setSpeedMotoreDxRotazione( 0 );
    delay(100);

    while (getRotazionePolsoDX() != destinazione) {
      t1 = millis();
      setSpeedMotoreDxRotazione( 
        constrain( 
          map(t1 - t0, 0, 1000, 0, -speed/3)
          ,-500 ,500) 
      );
    }
    setSpeedMotoreDxRotazione( 0 );

    angolo_mano_dx = destinazione;
  }
}

void ruotaManoSx(int destinazione) {
  int speed;
  unsigned long t0, t1;
  
  if (angolo_mano_sx != destinazione) {

    if ((angolo_mano_sx == DITO_CENTRALE_ALTO) && (destinazione == DITO_CENTRALE_LONTANO)) {
      speed = -FORZA_ROTAZIONE_MANO_SX;
    } else 
    if ((angolo_mano_sx == DITO_CENTRALE_LONTANO) && (destinazione == DITO_CENTRALE_BASSO)) {
      speed = -FORZA_ROTAZIONE_MANO_SX;
    } else 
    if ((angolo_mano_sx == DITO_CENTRALE_BASSO) && (destinazione == DITO_CENTRALE_VICINO)) {
      speed = -FORZA_ROTAZIONE_MANO_SX;
    } else 
    if ((angolo_mano_sx == DITO_CENTRALE_VICINO) && (destinazione == DITO_CENTRALE_ALTO)) {
      speed = -FORZA_ROTAZIONE_MANO_SX;
    } else {
      speed = FORZA_ROTAZIONE_MANO_SX;
    }
    setSpeedMotoreSxRotazione( speed );

    while (getRotazionePolsoSX() != 0) /* do nothing */;
    delay(50);

    while (getRotazionePolsoSX() != destinazione) /* do nothing */;
    t0 = millis();
    setSpeedMotoreSxRotazione( 0 );
    delay(100);

    while (getRotazionePolsoSX() != destinazione) {
      t1 = millis();
      setSpeedMotoreSxRotazione( 
        constrain( 
          map(t1 - t0, 0, 1000, 0, -speed/3)
          ,-500 ,500) 
      );
    }
    setSpeedMotoreSxRotazione( 0 );

    angolo_mano_sx = destinazione;
  }
}

void apriManoDx() {
  //setSpeedMotoreDxPresa( getJoystickDxY() );

}
void chiudiManoDx() {
  //setSpeedMotoreDxPresa( getJoystickDxY() );
    
}

void apriManoSx() {
  //setSpeedMotoreSxPresa( getJoystickSxY() );
    
}
void chiudiManoSx() {
  //setSpeedMotoreSxPresa( getJoystickSxY() );
    
}

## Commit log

2020-11-01 Motorino DC 3V
    [Motorino DC 3V v3.f3d, Motorino DC 3V v3.igs]
2021-01-17 Schematic & Library
    [shield-p1000 v8.f3z]
2021-01-17 Doc Arduino
    [dimensioniMega.dxf]
2021-02-05 DAC Generatore di funzioni
2021-03-28 PIN C INPUT
2021-04-18 WebServer con Arduino Mega e ESP-01S
2021-05-20 GERBER FILES #P1000
    [shield-p1000 v8.f3z, shield-p1000.brd, shield-p1000.sch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]
2021-06-12 FOTO PCB
2021-09-23 Modifiche al PCB
    [shield-p1000_v133.brd, shield-p1000_v53.sch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]
2021-10-28 prima prova di mano robotica
    [Componenti Mano.xls, base.stl, braccetto.stl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]
2021-11-04 Aggiornamento 04-11-2021
    [braccetto.stl, dito.stl]
2021-11-18 Aggiunto terzo dito
    [Componenti Mano.xls, base.stl, braccetto.stl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]
2021-11-25 encoder rotazione mano
    [Componenti Mano.xls, base.stl, mascherino_encoder.stl]
2021-12-09 aggiornamento 9-12-2021
    [Componenti Mano.xls, gancino2.stl, gancino3.stl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]
2021-12-16 modifiche 16 dicembre 2021
    [gancino1.stl, gancino2.stl, manovella.stl]
2021-12-23 Aggiunto encoder
    [martelletto.stl, polso.stl]
2022-01-13 Mano definitiva v60
    [Componenti Mano.xls, base.stl, braccetto.stl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]
2022-01-20 v65
    Aumentato spessore della parete esterna
    [base.stl, mascherino_encoder.stl, polso.stl]
2022-02-25 Completo carter
    [basamento robot 1.stl, basamento robot 2.stl, basamento robot 3.stl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]
2022-03-10 allargata fessura ingranaggio
    [polso.stl]
2022-06-23 con cuscinetti
    [342682_12mm_hex_wheel.stl, Componenti Mano.xls, base.stl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]
2024-07-08 ENCODER MANO
